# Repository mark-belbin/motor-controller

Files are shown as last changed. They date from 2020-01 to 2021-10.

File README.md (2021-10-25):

# FOC Motor Controller
This project was a multi-year effort to develop a ground-up, brushless motor (BLDC) controller for use in underwater robotics. 

The final controller is designed for T200 or T100 thrusters from BlueRobotics, boasting sensorless FOC and a miniature form-factor that is built right into the thruster.

## Key Features
- Sensorless FOC / sinusoidal commutation
- Input voltage up to 14V
- 250W Continuous Power
- CAN Bus telemetry and control
- Built into the T200 thruster, water-cooled
- Low underwater acoustic noise
- Up to 10-20% better efficiency than standard ESCs
- Great low-RPM operation and control
- *Ludicrous* mode, able to overmodulate and reach higher RPMs

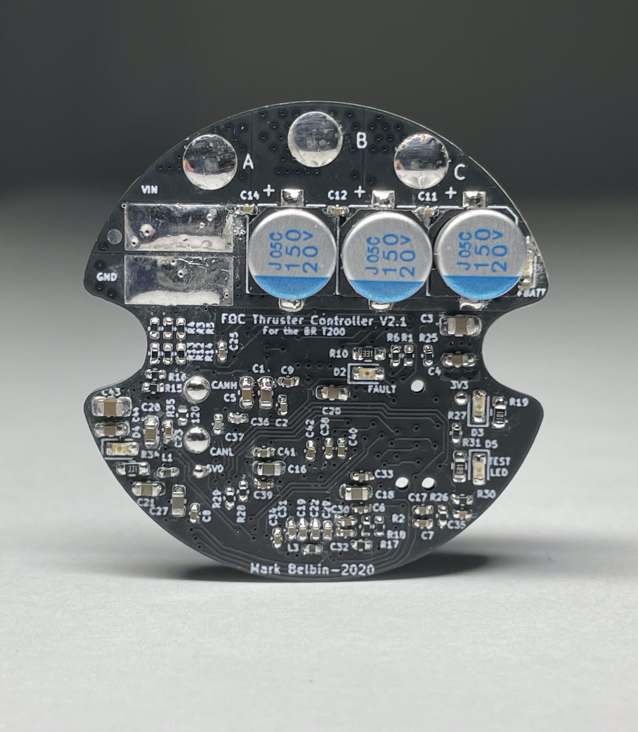
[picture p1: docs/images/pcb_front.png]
PCB Front


> FOC Thruster Controller V2 Top View

PCB Back

> FOC Thruster Controller V2 Bottom View

# Table of Contents
1. [Introduction](#Introduction)
1. [FOC Benefits](#FOC-Benefits)
   1. [Phase Currents](#Phase-Currents)
   1. [Operating Noise](#Operating-Noise)
   1. [Efficiency](#Efficiency)
   1. [Other Benefits](#Other-Benefits)
1. [Motor Controller PCB](#Motor-Controller-PCB)
1. [Controller Firmware](#Controller-Firmware)
1. [T200 Thruster Mount](#T200-Thruster-Mount)
1. [Repository Content](#Repository-Content)

# Introduction
Brushless motors, such as BLDC or PMSM motors, have no physical link between the stator and rotor like in a standard DC motor. Therefore, these motors must be commutated (spun properly) using an external controller. The key is knowing where the motor's rotor is relative to the stator, such that the magnetic field of the stator can be generated with accuracy in order to successfully push along the rotor and get the motor to spin. 

For most hobby BLDC controllers, commonly referred to as electronic speed controllers (ESCs), motor commutation is accomplished through sensorless trapezoidal 6-step control. This commutation method steps through 6 distinct stator magnetic field positions in order to keep the motor spinning, based only on the feedback of the back-EMF voltage of the three motor phases. With only 6 available control positions, this method of commutation lacks maximum possible efficiency, but it remains a simple, reliable, and cheap control method. 

This motor controller design implements Field-oriented control (FOC), also known as sinusoidal control or sine wave control. The FOC algorithm used is provided by Texas Instrument's InstaSPIN product line. This enables FOC using sensorless feedback, meaning no extra encoders or sensors are attached to the motor. The TI sensorless system measures only the 3 phase voltages and 3 phase currents of the motor in order to estimate the current rotor position with high accuracy. Also important is the intrinsic properties of the motor, such as the phase resistance, inductance, and the motor flux linkage. InstaSPIN requires a motor calibration procedure be run on each unique motor to automatically determine these intrinsic values, if not the FOC algorithm will not run.

This custom FOC controller design was evaluated by comparing against the BlueRobotics Basic ESC R3, a standard hobby-style ESC. Both will run the same BlueRobotics T200 thruster, which is the intended use-case of the custom developed controller. 

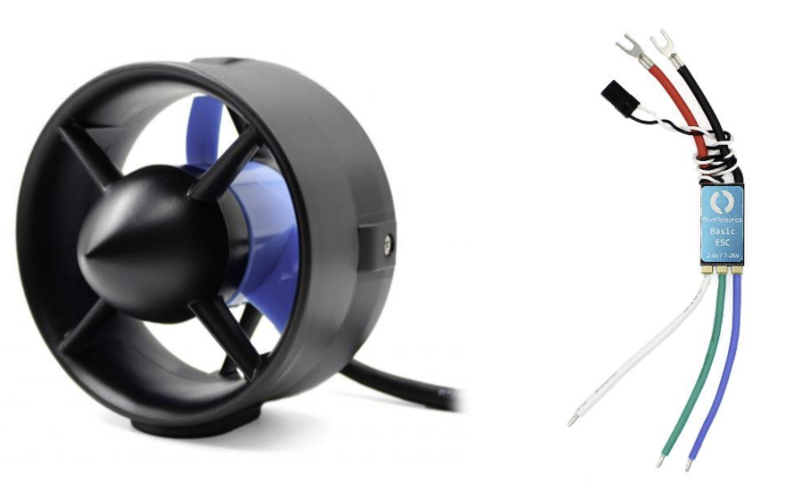
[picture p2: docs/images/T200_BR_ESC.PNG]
T200 and Basic ESC


> BlueRobotics T200 Thruster and Basic ESC R3.

# FOC Benefits
FOC has numerous potential benefits compared to traditional trapezoidal control. The most striking are the increase in efficiency and reduction in motor noise. This is possible since FOC control applies the most optimal stator magnetic field to push the rotor forward, and as a result generates clean and noise-free sine-wave current wave forms.

## Phase Currents

A comparison of current waveforms is shown below. Both the custom FOC controller and the Blue Robotics Basic ESC R3 are controlling a submerged T200 thruster at 2000 RPM. The FOC phase currents are much cleaner and closer to sinewaves, while the Basic ESC waveforms are more choppy and trapezoidal.

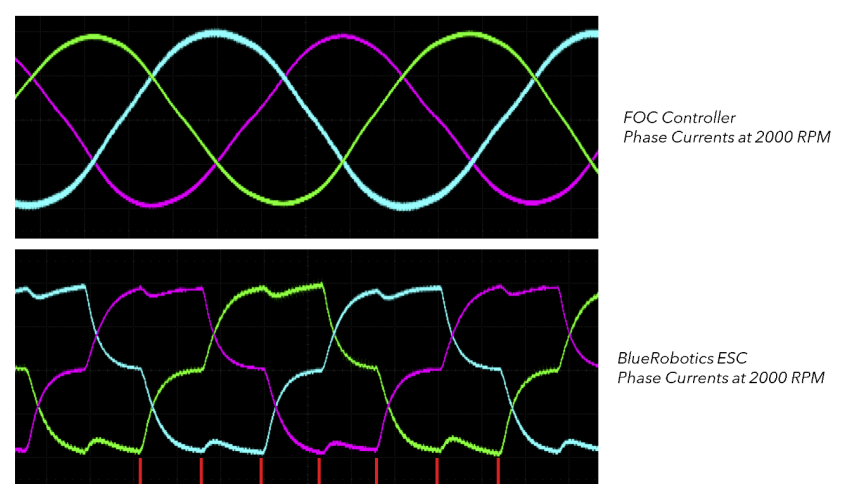
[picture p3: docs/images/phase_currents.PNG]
FOC Currents


> FOC phase currents vs the BR Basic ESC R3 at 2000 RPM.

## Operating Noise

A significant difference in operating noise is observed because of the current waveform difference. This is very noticeable underwater too, as the louder electrical sounds generated by the Basic ESC travel far. By comparison the custom FOC controller runs quiet, especially for low to mid-range speeds of 0-2000 RPM.

## Efficiency

An efficiency test was completed for both the custom and off-the-shelf controllers. A T200 was secured and submerged in a relatively large tub full of water. A separate waterproof, magnetic RPM sensor was attached to the shaft of the T200 to independently measure the RPM of the thruster. Measurements were taken of the input power of the motor controller under test for RPM settings in steps of 100 RPM.

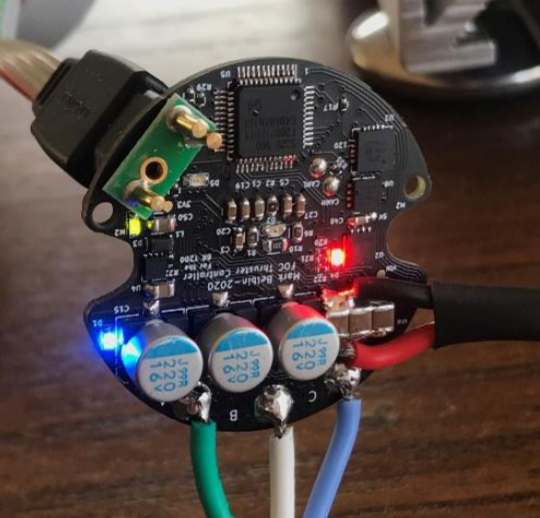
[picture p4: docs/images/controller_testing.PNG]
Controller Testing


> FOC Controller Testing

The FOC controller is more efficient across nearly the entire RPM range. The graph below is shows superiority up until about 2500 RPM, beyond which the FOC controller has the same or slightly worse performance. This is a limitation of FOC, where at a certain voltage the controller will switch to overmodulation control, where the controller will gradually transition to trapezoidal control as the RPM increases. To remain efficient at upper RPMs, a higher input voltage would need to be supplied.

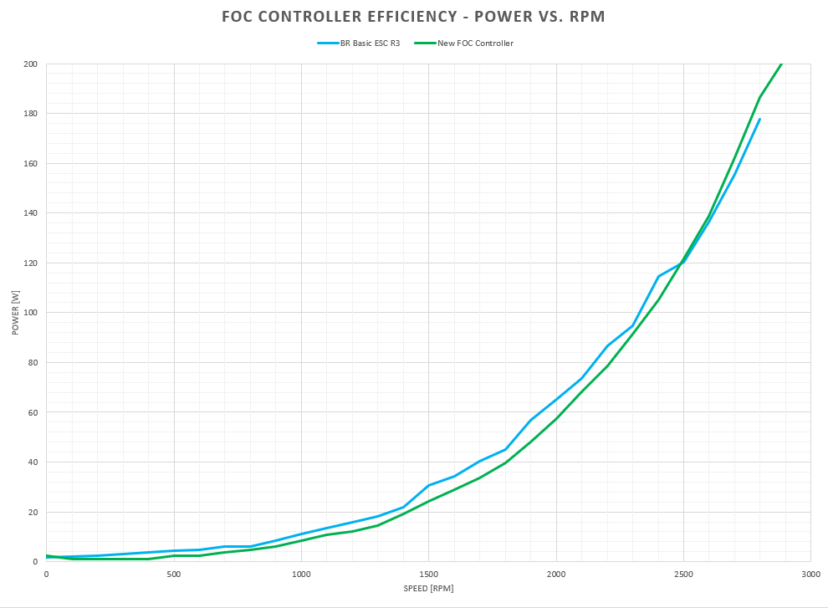
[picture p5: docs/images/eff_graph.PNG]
Efficiency Graph


> FOC Controller vs the BR Basic ESC R3.

Here's how the efficiency difference changes over the course of the RPM range: 

- From 0 to 600 RPM, the FOC controller consumes about 50% less power, a percent increase in efficiency of 100-150%
- From 600 to 1500 RPM, 20% less power is consumed, a percent increase in efficiency of 25-30%.
- From 1500 to 2000 RPM, 15% less power is consumed, a percent increase in efficiency of 15-20%.
- From 2000 to 2500 RPM, 5-10% less power is consumed, a percent increase in efficiency of 8-10%.
- Beyond 2500 RPM, the FOC controller consumes 0-5% more power than the Basic ESC.

The outperformance at lower RPMs is significant, since many underwater robotics applications operate in this range, such as Autonomous Underwater Vehicles (AUVs) or Autonomous Surface Vessels (ASVs). Battery life is critical for these types of vehicles, and the reduction in motor power from FOC control could have a big impact. 

## Other Benefits

A few other minor benefits were observed with the custom controller and FOC:

1. Great low speed control; The controller can operate at speeds down to a few RPM, where the Basic ESC cuts out under about 100 RPM.
2. Clean forward / reverse switching; During 0 RPM crossings, the FOC controller is much more stable, and can make these forward / reverse jumps with much quicker acceleration (about 25kRPM/s vs 14kRPM/s). This could improve position locking or increase accuracy for delicate maneuvers. 
3. *Ludicrous mode*; The FOC controller's overmodulation feature can push the thruster faster than the Basic ESC for the same input voltage, about 100 more RPM at 12V. Since thrust is proportional to the square of the RPM, this extra 100 RPM is a nice power boost.

# Motor Controller PCB
The motor controller PCB design was created using KiCAD. It's a 4 layer board, approximately in the shape of a xx diameter circle. The notches in the design allow it to be dropped in a mount for the T200 thruster. The PCB project is located in "hardware/Thruster_Controller_V2". An older version of the controller is found in "hardware/Thruster_Controller_V1", with the main difference being a different TI microcontroller.

PCB Angled

> FOC Thruster Controller V2 Angled View

The board itself is dense, and probably could have benefitted from a 6 layer design instead. However, limiting the design to 4 layers keeps the prototype costs very cheap. In total, for an order of 10 PCBAs, the total cost for the boards were about $2 each thanks to JLCPCB, and the total component cost is about $36.50 per board. So in total, less than $40 CAD per PCBA for only a 10 order quantity, not bad! At scale, this can shrink further, but probably not less than $25 per board.

Some major components are:
- TMS320F280041C -> TI microcontroller with InstaSPIN.
- DRV8320S -> Motor driver from TI.
- SIZF906DT -> Dual-MOSFETs in a compact package
- ATA6561 -> CAN Transceiver

# Controller Firmware
The controller firmware is based on MotorControl SDK 3.01 from TI. This SDK enables sensorless FOC with select TI microcontrollers. The microcontrollers have a proprietary InstaSPIN sensorless algorithm embedded in the ROM, which restricts this system to compatible TI MCUs only. 

The code is modified from a MotorControl SDK example lab, with extra drivers written for CAN communication. There is also some modification to disable a built-in overcurrent feature using the CMPSS. For whatever reason the feature seems to be bugged. I haven't yet figured out a good solution to either fix it or replace the overcurrent protection. So take caution if using this project as a base for something else! 

The IDE used is TIs Code Composer Studio, a customized version of Eclipse. The most up-to-date project is found in "firmware/TI_ESC_V2". The project is completely separated from TIs MotorControl SDK libraries, so it should be portable and importable in to Code Composer Studio from any computer with/without MotorControl SDK installed.

# T200 Thruster Mount
The motor controller PCBA was designed to be integrated into the back of the T200. The PCBA is first placed in an aluminum mount. Then, the thruster phase wires are soldered to the PCB. These wires are exposed by hacking away the jacket of the thruster very delicately. A new 10-conductor cable is then soldered to the PCB, replacing the original thruster cable. The final assembly is then potted, and mounted to the back of the thruster using the existing two screw holes originally for the back nose-cone. With this integration, the controller is water-cooled by the the thruster itself as water is forced passed it. 

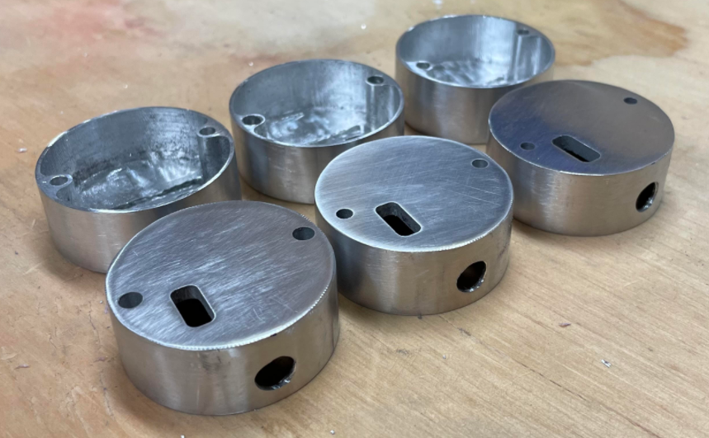
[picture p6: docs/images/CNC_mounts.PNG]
CNC Mounts


> Fresh-cut aluminum PCBA mounts

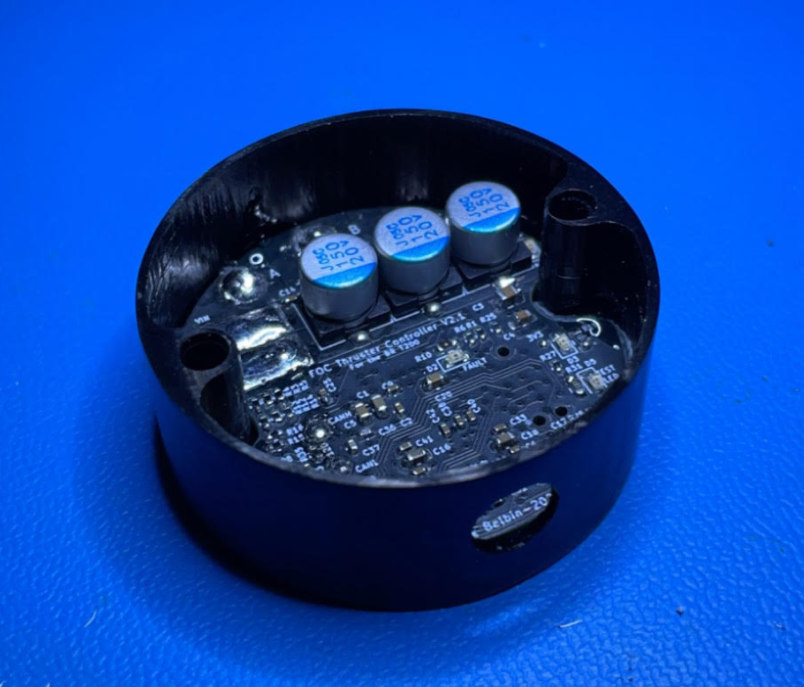
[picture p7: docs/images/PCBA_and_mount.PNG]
Controller Mount


> Anodized mount + PCBA

An interesting aspect of the mount design is the inclusion of a sealing disk. This disk, plus an o-ring, seals a programming port on the controller. This allows for reprogramming of the TI microcontroller while still maintaining water resistance. In the future it might be nice to include a bootloader on the microcontroller, which would allow programming over CAN instead, eliminating the need for this extra sealing disk! 

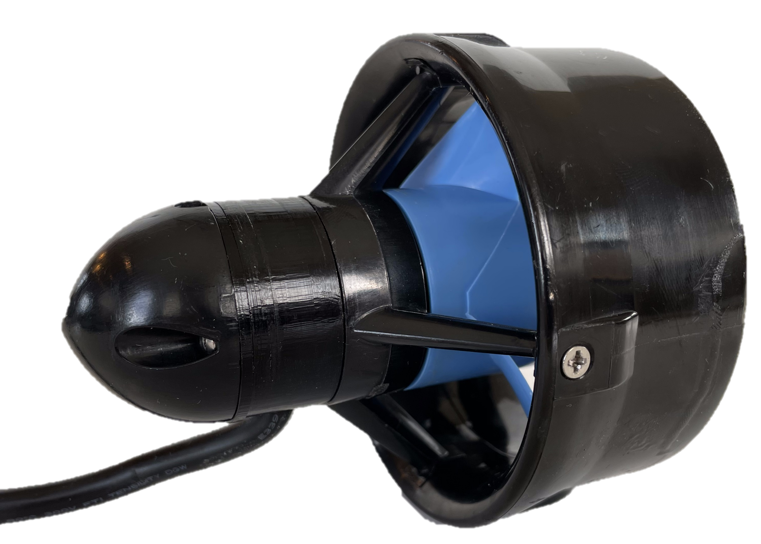
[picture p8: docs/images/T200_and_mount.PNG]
T200 + Controller Angled


> T200 + Controller Angled View

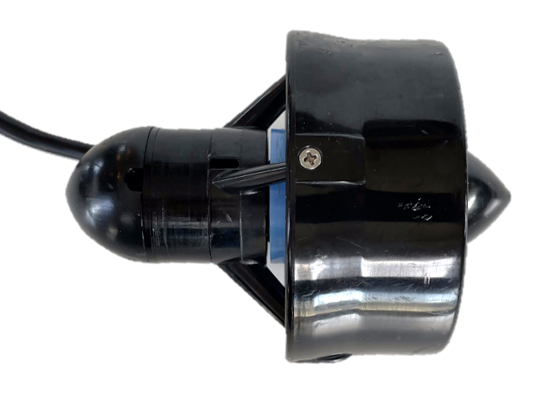
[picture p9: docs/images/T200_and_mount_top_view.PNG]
T200 + Controller Top


> T200 + Controller Top View

# AUV Integration

An immediate application of the FOC thruster controller was in my final-year engineering senior design project; an autonomous underwater vehicle (AUV). The AUV includes six thrusters in the design, and I built an FOC controller in each one. In the end, the project was a resounding success, and a very good test scenario for the custom controllers. The controllers were smooth, operating well at low speeds, which is all the AUV needed. The thrusters also operated very quietly, even when pushing the AUV to higher speeds for fun. 

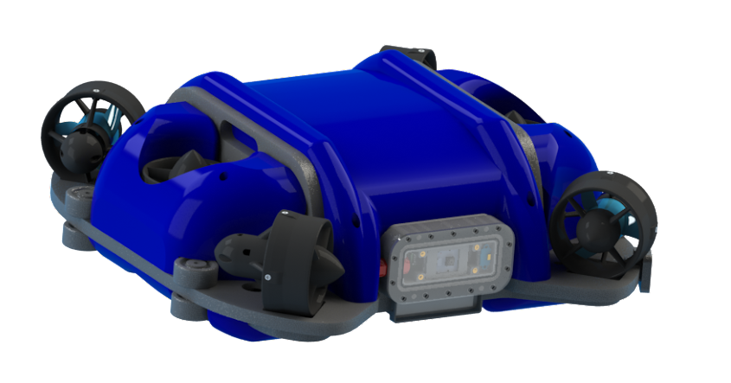
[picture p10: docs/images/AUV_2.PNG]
AUV Top


> Capstone AUV Top View

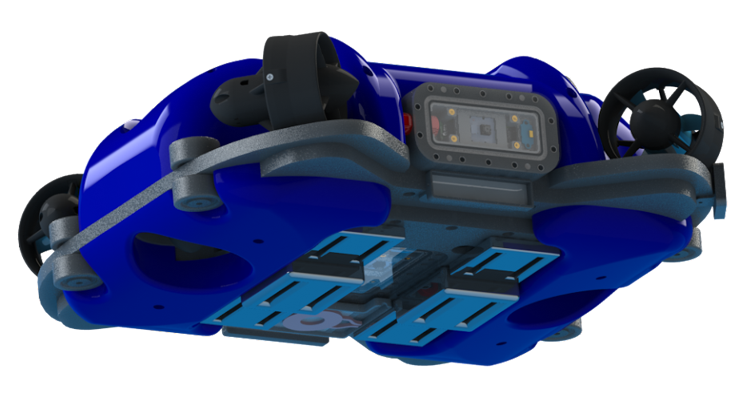
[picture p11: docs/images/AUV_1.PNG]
AUV Bottom


>  Capstone AUV Bottom View

Check out the AUV in action here -> https://www.youtube.com/watch?v=-c5bOXZom5M

# Repository Content
The repository is organized into 3 categories; hardware, firmware, and docs. Included in the hardware folder is the latest FOC controller V2, as well as an older version V1, and many test boards built to test and evaluate the project along the way. The firmware folder includes the latest V2 firmware, as well as the V1 firmware and sample test projects that were provided by TI and were useful for debugging.

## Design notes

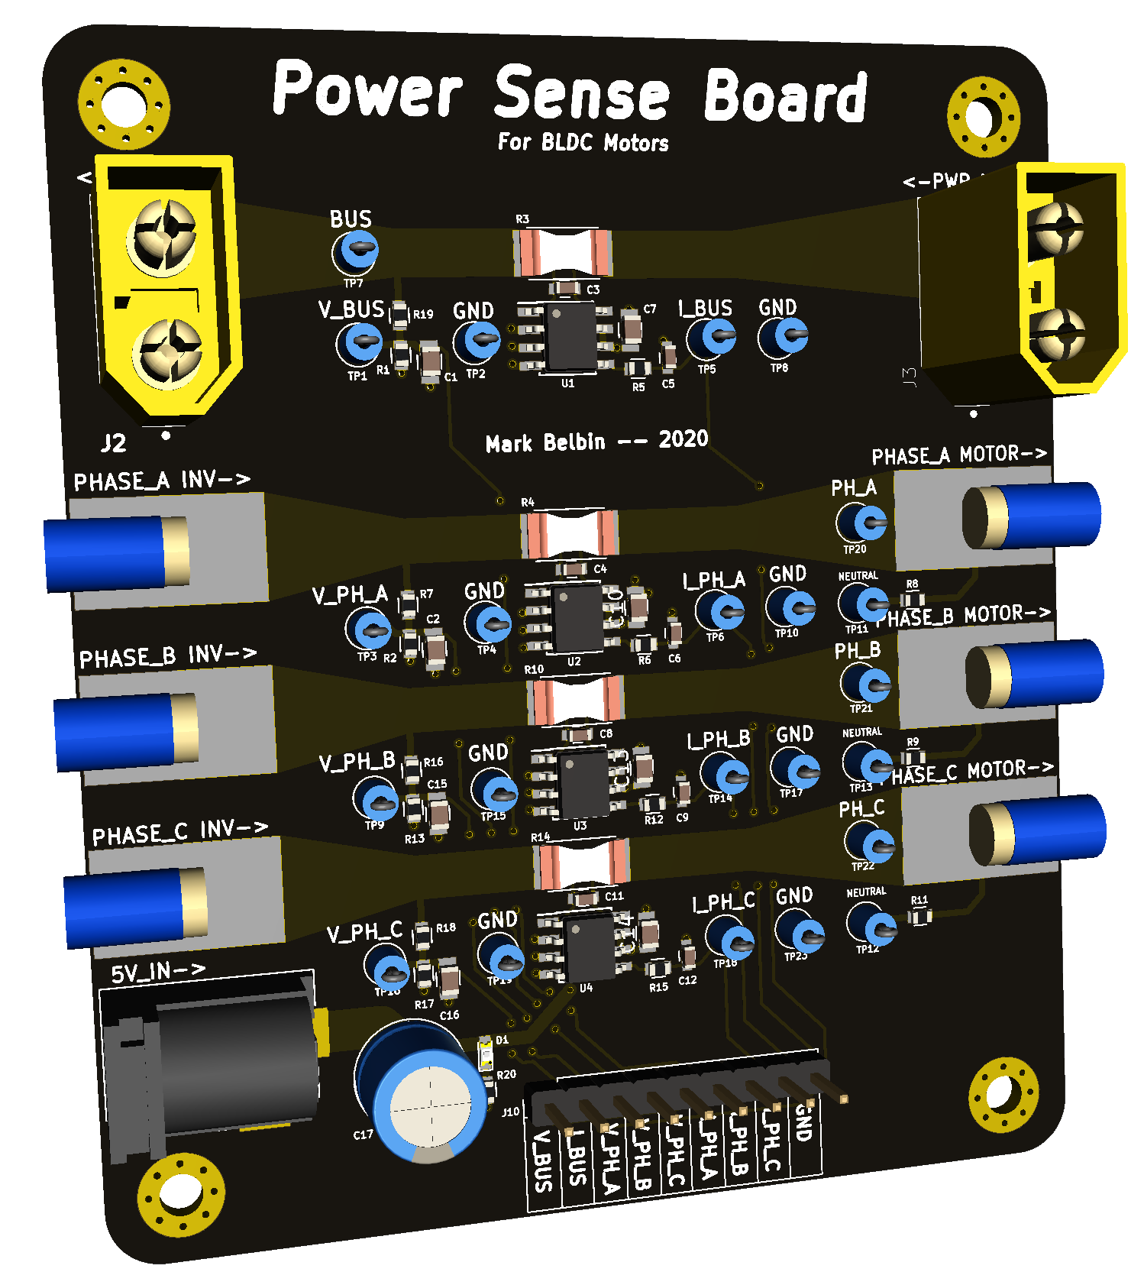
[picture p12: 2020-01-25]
hardware/Power Sense PCB/3D View.PNG

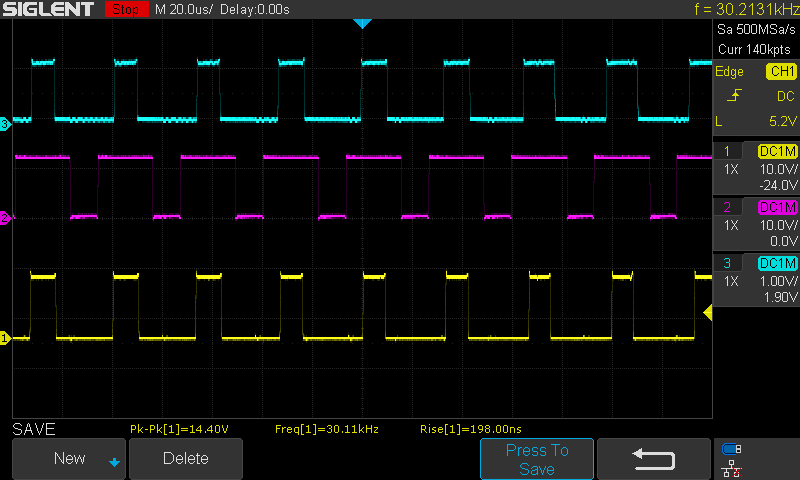
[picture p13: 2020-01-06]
hardware/ESC Drivetrain V1/Scope Shots/SDS00005.png

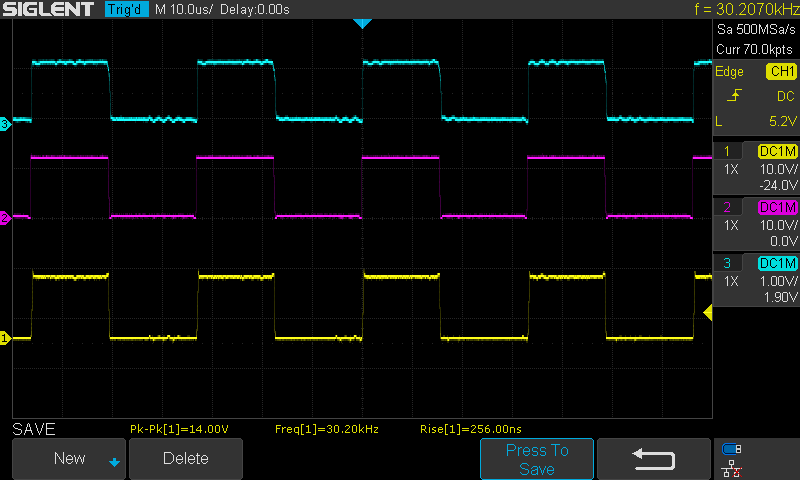
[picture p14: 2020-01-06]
hardware/ESC Drivetrain V1/Scope Shots/SDS00001.png

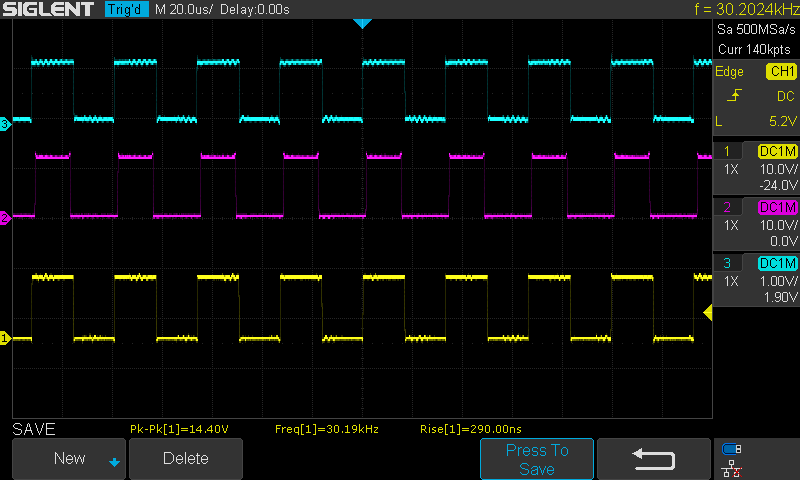
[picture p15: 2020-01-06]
hardware/ESC Drivetrain V1/Scope Shots/SDS00006.png

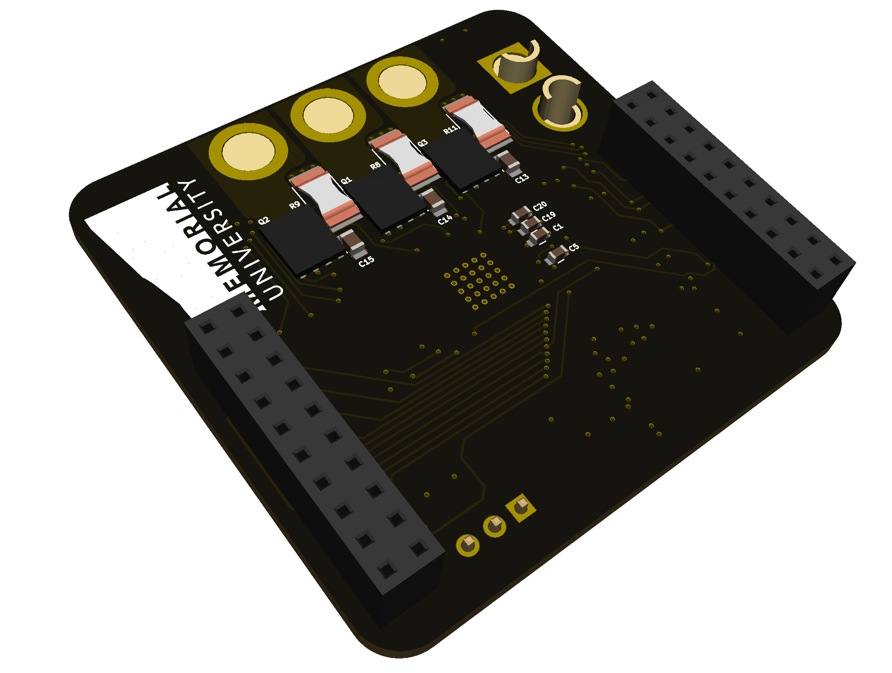
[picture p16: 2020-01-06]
hardware/ESC Drivetrain V1/3D View 2.PNG

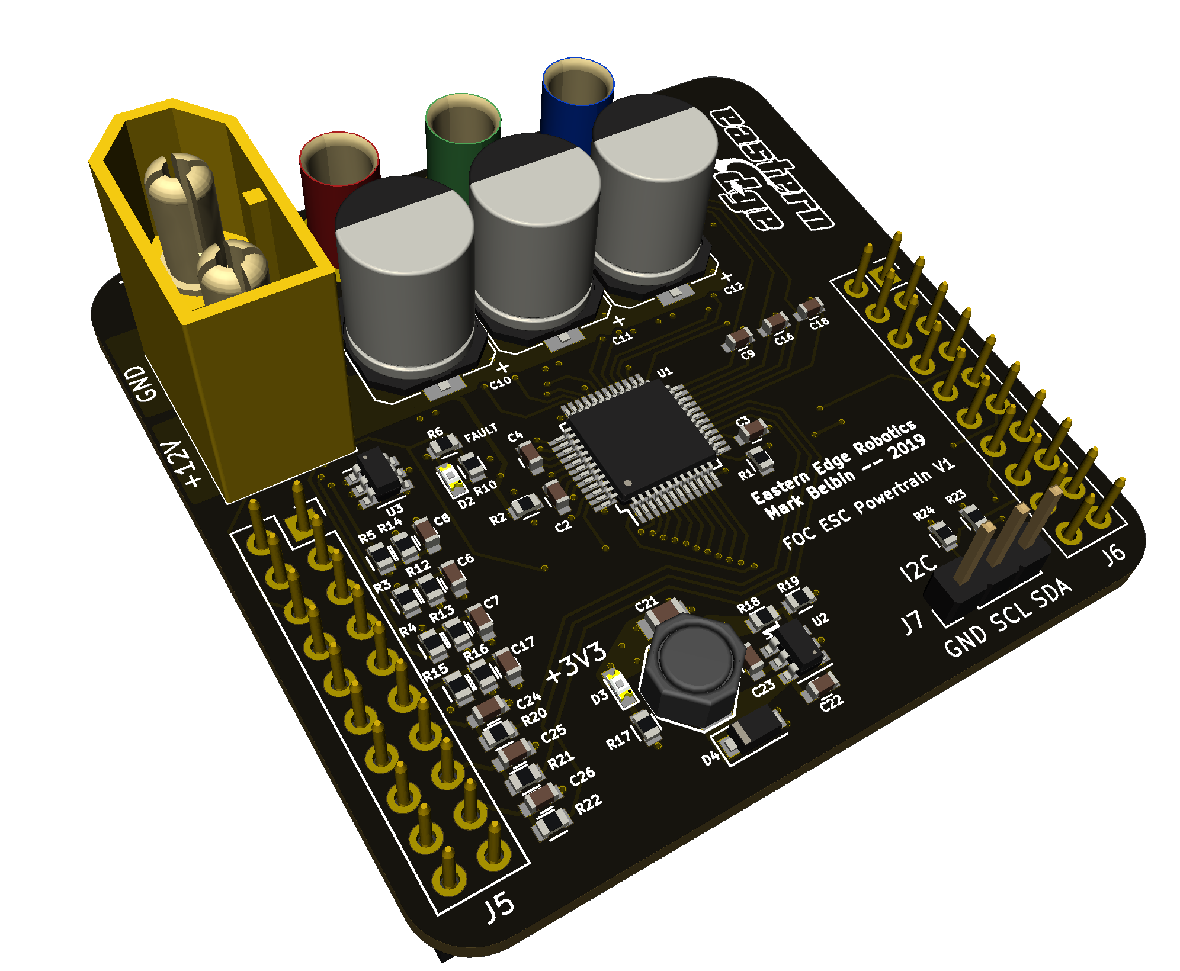
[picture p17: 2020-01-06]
hardware/ESC Drivetrain V1/3D View 1.PNG

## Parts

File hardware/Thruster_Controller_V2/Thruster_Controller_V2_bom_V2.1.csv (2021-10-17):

Component | Description | Part | References | Value | Footprint | Quantity Per PCB | Datasheet | Digikey | Voltage | Mouser
1 | Unpolarized capacitor, small symbol | C_Small | C11 C12 C14 C35 | 0.01uF | C_0402_1005Metric | 4 |  | 732-7545-1-ND
2 | Unpolarized capacitor, small symbol | C_Small | C2 | 0.047uF | C_0402_1005Metric | 1 |  | 490-10702-1-ND
3 | Unpolarized capacitor, small symbol | C_Small | C6 C7 C8 C9 C17 C23 C31 C33 C34 C38 C39 C40 C41 C42 | 0.1uF | C_0402_1005Metric | 14 |  | 490-10698-1-ND
4 | Unpolarized capacitor, small symbol | C_Small | C16 C18 C21 C27 | 10uF | C_0603_1608Metric | 4 | ~ | 1276-1119-1-ND
5 | Unpolarized capacitor, small symbol | C_Small | C4 C5 C20 C28 C44 | 1uF | C_0603_1608Metric | 5 |  | 1276-1102-1-ND
6 | Unpolarized capacitor, small symbol | C_Small | C3 C43 | 1uF | C_0805_2012Metric | 2 |  | 1276-6470-1-ND | 50V
7 | Unpolarized capacitor, small symbol | C_Small | C19 C22 C29 C30 C32 | 2.2uF | C_0402_1005Metric | 5 | ~ | 490-10451-1-ND
8 | Unpolarized capacitor, small symbol | C_Small | C24 C25 C26 | 2200pF | C_0402_1005Metric | 3 |  | 490-6359-1-ND
9 | Unpolarized capacitor | C | C10 C13 C15 | 220uF | CP_Elec_6.3x5.8 | 3 | ~ | 565-APXJ160ARA221MF61GCT-ND
10 | Unpolarized capacitor, small symbol | C_Small | C1 | 4.7uF | C_0603_1608Metric | 1 |  | 1276-1900-1-ND
11 | Unpolarized capacitor, small symbol | C_Small | C36 C37 | 9pF | C_0402_1005Metric | 2 | ~ | 490-5880-1-ND
12 | Light emitting diode, filled shape | LED_ALT | D1 | BLUE | LED_0603_1608Metric | 1 | ~ | 732-4966-1-ND
13 | Light emitting diode, filled shape | LED_ALT | D3 D4 | GREEN | LED_0603_1608Metric | 2 | ~ | 732-4980-1-ND
14 | Light emitting diode, filled shape | LED_ALT | D5 | Orange | LED_0603_1608Metric | 1 | ~ | 160-1180-1-ND
15 | Light emitting diode, filled shape | LED_ALT | D2 | RED | LED_0603_1608Metric | 1 | ~ | 732-4978-1-ND
16 | Generic connector, single row, 01x01, script generated (kicad-library-utils/schlib/autogen/connector/) | Conn_01x01 | J4 J6 | Conn_01x01 | CAN_Pad | 2 | ~
17 | Generic connector, single row, 01x01, script generated (kicad-library-utils/schlib/autogen/connector/) | Conn_01x01 | J7 J8 | Conn_01x01 | Bus_Pad | 2 | ~
18 | Generic connector, single row, 01x01, script generated (kicad-library-utils/schlib/autogen/connector/) | Conn_01x01 | J1 J2 J3 | PHASE_A | Phase_Pad | 3 | ~
19 | Generic connector, double row, 02x05, odd/even pin numbering scheme (row 1 odd numbers, row 2 even numbers), script generated (kicad-library-utils/schlib/autogen/connector/) | Conn_02x05_Odd_Even | J5 | Pogo Conn | Tag-Connect_TC2050-IDC-NL | 1 | ~
20 | Inductor, small symbol | L_Small | L1 | 220 Ohm | L_0402_1005Metric | 1 | ~ | 490-11021-1-ND
21 | Inductor, small symbol | L_Small | L3 | 60 Ohm | L_0402_1005Metric | 1 | ~ | 445-172882-1-ND
22 | Net tie, 2 pins | Net-Tie_2 | NT1 NT2 NT3 NT4 NT5 NT6 | Net-Tie_2 | NetTie-2_SMD_5mil | 6 | ~
23 |  | SIZF906DT | Q1 Q2 Q3 | SIZF906DT | SIZF906DT | 3 | http://www.vishay.com/docs/67547/sizf906dt.pdf | SIZF906DT-T1-GE3CT-ND
24 | Resistor, US symbol | R_US | R19 | 100 | R_0603_1608Metric | 1 | ~ | 2019-RK73B1JTTD101JCT-ND
25 | Resistor, US symbol | R_US | R6 R25 R26 R28 R29 | 10k | R_0402_1005Metric | 5 | ~ | 2019-RK73B1ETTP103JCT-ND
26 | Resistor, small US symbol | R_Small_US | R35 | 120 | R_0402_1005Metric | 1 | ~ | 311-120JRCT-ND
27 | Resistor, small US symbol | R_Small_US | R1 R27 R30 | 2.2k | R_0402_1005Metric | 3 | ~ | 311-2.2KJRCT-ND
28 | Resistor, US symbol | R_US | R23 R24 R32 | 2.49k | R_0402_1005Metric | 3 | ~ | RMCF0402FT2K49CT-ND
29 | Resistor, US symbol | R_US | R7 | 2.7k | R_0603_1608Metric | 1 | ~ | RMCF0603JT2K70CT-ND
30 | Resistor, US symbol | R_US | R3 R4 R5 R15 | 22.0k | R_0402_1005Metric | 4 | ~ | RMCF0402FT22K0CT-ND
31 | Resistor, US symbol | R_US | R34 | 220 | R_0603_1608Metric | 1 | ~ | 2019-RK73B1JTTD221JCT-ND
32 | Resistor, US symbol | R_US | R2 R17 R18 | 27.4k | R_0402_1005Metric | 3 | ~ | RMCF0402FT27K4CT-ND
33 | Resistor, US symbol | R_US | R10 | 330 | R_0603_1608Metric | 1 | ~ | RMCF0603JT330RCT-ND
34 | Resistor, US symbol | R_US | R12 R13 R14 R16 | 4.99k | R_0402_1005Metric | 4 | ~ | 311-4.99KLRCT-ND
35 | Resistor, US symbol | R_US | R20 R21 R22 R33 | 56 | R_0402_1005Metric | 4 | ~ | 311-56JRCT-ND
36 | Resistor, US symbol | R_US | R8 R9 R11 | 5m | R_2512_6332Metric | 3 |  | YAG6105CT-ND
37 | Resistor, US symbol | R_US | R31 | 680 | R_0603_1608Metric | 1 | ~ | RMCF0603JT680RCT-ND
38 | High-Speed CAN Transceiver, 1Mbps, 5V supply, Vio pin, -40C to +125C, DFN-8 | MCP2562-E-MF | U8 | ATA6561 | DFN-8-1EP_3x3mm_P0.65mm_EP1.7x2.05mm | 1 | https://ww1.microchip.com/downloads/en/DeviceDoc/20005991B.pdf | ATA6561-GBQW-NCT-ND |  | 579-ATA6561-GBQW-N
39 |  | DRV8320S | U3 | DRV8320S | WQFN-32-1EP_5x5mm_P0.5mm_EP3.1x3.1mm | 1 | http://www.ti.com/lit/ds/symlink/drv8323r.pdf?HQS=TI-null-null-mousermode-df-pf-null-wwe&DCM=yes&distId=26 | 296-50725-1-ND |  | 595-DRV8320SRTVR
40 |  | NCP718AMT330 | U1 | NCP718AMT330 | DFN-6-1EP_2x2mm_P0.65mm_EP1x1.6mm | 1 | https://www.mouser.ca/datasheet/2/308/NCP718-D-1224359.pdf | NCP718AMT330TBGOSCT-ND |  | 863-NCP718AMT330TBG
41 |  | NCP718AMT330 | U4 | NCP718AMT500 | DFN-6-1EP_2x2mm_P0.65mm_EP1x1.6mm | 1 | https://www.onsemi.com/pub/Collateral/NCP718-D.PDF | ‎NCP718AMT500TBGOSCT-ND‎ |  | 863-NCP718BMT500TBG
42 |  | TMS320F280041C | U2 | TMS320F280041C | QFN-56-1EP_7x7mm_P0.4mm_EP5.6x5.6mm | 1 | http://www.ti.com/lit/ds/symlink/tms320f280041.pdf?ts=1588432897241 | 296-F280041CRSHSRCT-ND |  | 595-F280041CRSHSR
43 | Three pin crystal, GND on pin 2 | Crystal_GND2 | Y1 | 20 MHz | Crystal_SMD_SeikoEpson_FA238-4pin_3.2x2.5mm | 1 | ~ | SER3629CT-ND
Component Groups: | 43
Component Count: | 109
Fitted Components: | 109
Number of PCBs: | 1
Total components: | 109
Schematic Version: | V2.1
Schematic Date: | 2020-09-04
PCB Variant: | [u'default']
BoM Date: | 2021-05-12 3:15:47 PM
Schematic Source: | D:\FOC_Motor_Controller\motor-controller\PCBs\Thruster_Controller_V2\Thruster_Controller_V2.sch
KiCad Version: | Eeschema (5.1.9)-1

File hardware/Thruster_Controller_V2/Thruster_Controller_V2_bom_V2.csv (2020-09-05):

Component | Description | Part | References | Value | Footprint | Quantity Per PCB | Datasheet | Digikey | Voltage | Mouser
1 | Unpolarized capacitor, small symbol | C_Small | C11 C12 C14 C35 | 0.01uF | C_0402 | 4 |  | 732-7545-1-ND
2 | Unpolarized capacitor, small symbol | C_Small | C2 | 0.047uF | C_0402 | 1 |  | 490-10702-1-ND
3 | Unpolarized capacitor, small symbol | C_Small | C6 C7 C8 C9 C17 C23 C31 C33 C34 C38 C39 C40 C41 C42 | 0.1uF | C_0402 | 14 |  | 490-10698-1-ND
4 | Unpolarized capacitor, small symbol | C_Small | C16 C18 C21 C27 | 10uF | C_0603 | 4 | ~ | 1276-1119-1-ND
5 | Unpolarized capacitor, small symbol | C_Small | C4 C5 C20 C28 | 1uF | C_0603 | 4 |  | 1276-1102-1-ND
6 | Unpolarized capacitor, small symbol | C_Small | C3 | 1uF | C_0805 | 1 |  | 1276-6470-1-ND | 50V
7 | Unpolarized capacitor, small symbol | C_Small | C19 C22 C29 C30 C32 | 2.2uF | C_0402 | 5 | ~ | 490-10451-1-ND
8 | Unpolarized capacitor, small symbol | C_Small | C24 C25 C26 | 2200pF | C_0402 | 3 |  | 490-6359-1-ND
9 | Unpolarized capacitor | C | C10 C13 C15 | 220uF | CP_Elec_6.3x5.8 | 3 | ~ | 565-APXJ160ARA221MF61GCT-ND
10 | Unpolarized capacitor, small symbol | C_Small | C1 | 4.7uF | C_0603 | 1 |  | 1276-1900-1-ND
11 | Unpolarized capacitor, small symbol | C_Small | C36 C37 | 9pF | C_0402 | 2 | ~ | 490-5880-1-ND
12 | Light emitting diode, filled shape | LED_ALT | D1 | BLUE | LED_0603 | 1 | ~ | 732-4966-1-ND
13 | Light emitting diode, filled shape | LED_ALT | D3 | GREEN | LED_0603 | 1 | ~ | 732-4980-1-ND
14 | Light emitting diode, filled shape | LED_ALT | D5 | Orange | LED_0603 | 1 | ~ | 160-1180-1-ND
15 | Light emitting diode, filled shape | LED_ALT | D2 | RED | LED_0603 | 1 | ~ | 732-4978-1-ND
16 | Generic connector, single row, 01x01, script generated (kicad-library-utils/schlib/autogen/connector/) | Conn_01x01 | J4 J6 | Conn_01x01 | CAN_Pad | 2 | ~
17 | Generic connector, single row, 01x01, script generated (kicad-library-utils/schlib/autogen/connector/) | Conn_01x01 | J7 J8 | Conn_01x01 | Bus_Pad | 2 | ~
18 | Generic connector, single row, 01x01, script generated (kicad-library-utils/schlib/autogen/connector/) | Conn_01x01 | J1 J2 J3 | PHASE_A | Phase_Pad | 3 | ~
19 | Generic connector, double row, 02x05, odd/even pin numbering scheme (row 1 odd numbers, row 2 even numbers), script generated (kicad-library-utils/schlib/autogen/connector/) | Conn_02x05_Odd_Even | J5 | Pogo Conn | Tag-Connect_TC2050-IDC-NL | 1 | ~
20 | Inductor, small symbol | L_Small | L1 | 220 Ohm | L_0402 | 1 | ~ | 490-11021-1-ND
21 | Inductor, small symbol | L_Small | L3 | 60 Ohm | L_0402 | 1 | ~ | 445-172882-1-ND
22 | Net tie, 2 pins | Net-Tie_2 | NT1 NT2 NT3 NT4 NT5 NT6 | Net-Tie_2 | NetTie-2_SMD_5mil | 6 | ~
23 |  | SIZF906DT | Q1 Q2 Q3 | SIZF906DT | SIZF906DT | 3 | http://www.vishay.com/docs/67547/sizf906dt.pdf | SIZF906DT-T1-GE3CT-ND
24 | Resistor, US symbol | R_US | R6 R25 R26 R28 R29 | 10k | R_0402 | 5 | ~ | 2019-RK73B1ETTP103JCT-ND
25 | Resistor, small US symbol | R_Small_US | R35 | 120 | R_0402 | 1 | ~ | 311-120JRCT-ND
26 | Resistor, US symbol | R_US | R19 | 180 | R_0603 | 1 | ~ | 2019-RK73B1JTTD181JCT-ND
27 | Resistor, small US symbol | R_Small_US | R1 R27 R30 | 2.2k | R_0402 | 3 | ~ | 311-2.2KJRCT-ND
28 | Resistor, US symbol | R_US | R23 R24 R32 | 2.49k | R_0402 | 3 | ~ | RMCF0402FT2K49CT-ND
29 | Resistor, US symbol | R_US | R7 | 2.7k | R_0603 | 1 | ~ | RMCF0603JT2K70CT-ND
30 | Resistor, US symbol | R_US | R3 R4 R5 R15 | 22.0k | R_0402 | 4 | ~ | RMCF0402FT22K0CT-ND
31 | Resistor, US symbol | R_US | R2 R17 R18 | 27.4k | R_0402 | 3 | ~ | RMCF0402FT27K4CT-ND
32 | Resistor, US symbol | R_US | R10 | 330 | R_0603 | 1 | ~ | RMCF0603JT330RCT-ND
33 | Resistor, US symbol | R_US | R12 R13 R14 R16 | 4.99k | R_0402 | 4 | ~ | 311-4.99KLRCT-ND
34 | Resistor, US symbol | R_US | R20 R21 R22 R33 | 56 | R_0402 | 4 | ~ | 311-56JRCT-ND
35 | Resistor, US symbol | R_US | R8 R9 R11 | 5m | R_2512 | 3 |  | YAG6105CT-ND
36 | Resistor, US symbol | R_US | R31 | 680 | R_0603 | 1 | ~ | RMCF0603JT680RCT-ND
37 |  | DRV8320S | U3 | DRV8320S | WQFN-32-1EP_5x5mm_Pitch0.5mm | 1 | http://www.ti.com/lit/ds/symlink/drv8323r.pdf?HQS=TI-null-null-mousermode-df-pf-null-wwe&DCM=yes&distId=26 | 296-50725-1-ND |  | 595-DRV8320SRTVR
38 | High-Speed CAN Transceiver, 1Mbps, 5V supply, Vio pin, -40C to +125C, DFN8 package | MCP2562-E-MF | U8 | MCP2562 | DFN-8-1EP_3x3mm_Pitch0.65mm | 1 | http://ww1.microchip.com/downloads/en/DeviceDoc/25167A.pdf | MCP2562-E/MF-ND
39 |  | NCP718AMT330 | U1 | NCP718AMT330 | DFN-6-1EP_2x2mm_Pitch0.65mm | 1 | https://www.mouser.ca/datasheet/2/308/NCP718-D-1224359.pdf | NCP718AMT330TBGOSCT-ND |  | 863-NCP718AMT330TBG
40 |  | TMS320F280041C | U2 | TMS320F280041C | QFN-56-1EP_7x7mm_Pitch0.4mm | 1 | http://www.ti.com/lit/ds/symlink/tms320f280041.pdf?ts=1588432897241 | 296-F280041CRSHSRCT-ND |  | 595-F280041CRSHSR
41 | Three pin crystal, GND on pin 2 | Crystal_GND2 | Y1 | 20 MHz | Crystal_SMD_SeikoEpson_FA238-4pin_3.2x2.5mm | 1 | ~ | SER3629CT-ND
Component Groups: | 41
Component Count: | 104
Fitted Components: | 104
Number of PCBs: | 1
Total components: | 104
Schematic Version: | V2
Schematic Date: | 2020-08-22
PCB Variant: | [u'default']
BoM Date: | 2020-08-22 4:44:00 PM
Schematic Source: | D:\Motor Controller Research\GitHub\motor-controller\PCBs\Thruster_Controller_V2\Thruster_Controller_V2.sch
KiCad Version: | Eeschema (5.1.5)-3

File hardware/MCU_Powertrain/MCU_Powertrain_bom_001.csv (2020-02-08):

Component | Description | Part | References | Value | Footprint | Quantity Per PCB | Datasheet | Digikey | Voltage
1 | Unpolarized capacitor, small symbol | C_Small | C2 C4 | 0.047uF | C_0402 | 2 |  | 490-10702-1-ND
2 | Unpolarized capacitor, small symbol | C_Small | C6 C7 C8 C17 C23 C30 C33 C42 | 0.1uF | C_0603 | 8 |  | 1276-CL10B104KB8NNNLCT-ND
3 | Unpolarized capacitor, small symbol | C_Small | C32 | 0.33uF | C_0603 | 1 |  | 1276-2370-1-ND
4 | Unpolarized capacitor, small symbol | C_Small | C39 | 1.01uF | C_0805 | 1 |  | 311-1909-1-ND | 35V
5 | Unpolarized capacitor, small symbol | C_Small | C9 C16 C18 | 1000pF | C_0402 | 3 |  | 311-1036-1-ND
6 | Unpolarized capacitor, small symbol | C_Small | C21 C22 | 15pF | C_0603 | 2 | ~ | 311-1060-1-ND
7 | Unpolarized capacitor, small symbol | C_Small | C3 C5 C20 C27 | 1uF | C_0603 | 4 |  | 1276-1102-1-ND
8 | Unpolarized capacitor, small symbol | C_Small | C28 C29 C40 C41 | 1uF | C_0805 | 4 |  | 399-8011-1-ND
9 | Unpolarized capacitor, small symbol | C_Small | C19 | 2.2uF | C_0603 | 1 |  | 490-10731-1-ND
10 | Unpolarized capacitor, small symbol | C_Small | C34 C35 C36 C37 C38 | 2.2uF | C_0805 | 5 | ~ | 1276-1763-1-ND
11 | Unpolarized capacitor, small symbol | C_Small | C24 C25 C26 | 2200pF | C_0603 | 3 |  | 490-1459-1-ND
12 | Polarized capacitor, US symbol | CP1 | C10 C11 C12 | 220uF | CP_Elec_8x10.5 | 3 |  | 25PEV220M8X10.5CT-ND
13 | Unpolarized capacitor, small symbol | C_Small | C13 C14 C15 C31 | 22uF | C_0805 | 4 |  | 490-14661-1-ND
14 | Unpolarized capacitor, small symbol | C_Small | C1 | 4.7uF | C_0603 | 1 |  | 1276-1900-1-ND
15 | Light emitting diode, filled shape | LED_ALT | D1 | BLUE | LED_0603 | 1 | ~ | 160-1827-1-ND
16 | Light emitting diode | LED | D5 D6 D7 D8 | BLUE | LED_0805 | 4 | ~ | 732-4982-1-ND
17 | Schottky diode, filled shape | D_Schottky_ALT | D4 | D_Schottky_ALT | D_SOD-123F | 1 | ~ | MBR1H100SFT3GOSCT-ND
18 | Light emitting diode, filled shape | LED_ALT | D3 | GREEN | LED_0603 | 1 | ~ | 160-1446-1-ND
19 | Light emitting diode, filled shape | LED_ALT | D2 | RED | LED_0603 | 1 | ~ | 160-1447-1-ND
20 | Generic connector, double row, 02x05, odd/even pin numbering scheme (row 1 odd numbers, row 2 even numbers), script generated (kicad-library-utils/schlib/autogen/connector/) | Conn_02x05_Odd_Even | J4 | Big Conn | 2x05_Prog_Header | 1 | ~ | 302-S101
21 | Generic connector, single row, 01x03, script generated (kicad-library-utils/schlib/autogen/connector/) | Conn_01x03 | J6 | Conn CAN | 70553-03 | 1 | ~ | WM4901-ND
22 | Generic connector, single row, 01x01, script generated (kicad-library-utils/schlib/autogen/connector/) | Conn_01x01 | J1 J2 J3 | PHASE_A | 3mm_Bullet_RA | 3 | ~
23 | Generic connector, single row, 01x02, script generated (kicad-library-utils/schlib/autogen/connector/) | Conn_01x02 | J7 | PWRIN | AMASS_XT60-M | 1 | ~
24 | Generic connector, double row, 02x05, odd/even pin numbering scheme (row 1 odd numbers, row 2 even numbers), script generated (kicad-library-utils/schlib/autogen/connector/) | Conn_02x05_Odd_Even | J5 | Pogo Conn | Tag-Connect_TC2050-IDC-NL | 1 | ~
25 | Inductor with ferrite core | L_Core_Ferrite | L1 | 15uH | Eaton_Inductor | 1 | ~ | 513-1458-1-ND
26 | Inductor, small symbol | L_Small | L2 | FB | L_0805 | 1 | ~ | 240-2549-1-ND
27 | Inductor, small symbol | L_Small | L3 | FB | L_0402 | 1 | ~ | 445-172882-1-ND
28 | Net tie, 2 pins | Net-Tie_2 | NT1 NT2 NT3 NT4 NT5 NT6 | Net-Tie_2 | NetTie-2_SMD_5mil | 6 | ~
29 |  | SIZF906DT | Q1 Q2 Q3 | SIZF906DT | SIZF906DT | 3 | http://www.vishay.com/docs/67547/sizf906dt.pdf | SIZF906DT-T1-GE3CT-ND
30 | Resistor, US symbol | R_US | R2 | 100 | R_0603 | 1 | ~ | RHM100DCT-ND
31 | Resistor, US symbol | R_US | R1 R6 | 10k | R_0603 | 2 | ~ | RNCP0603FTD10K0CT-ND
32 | Resistor, small US symbol | R_Small_US | R17 R18 | 10k | R_0805 | 2 | ~ | 311-10.0KCRCT-ND
33 | Resistor, small US symbol | R_Small_US | R35 | 120 | R_0805 | 1 | ~ | A129738CT-ND
34 | Resistor, small US symbol | R_Small_US | R27 R28 R29 R30 | 2.2k | R_0805 | 4 | ~ | 541-4139-1-ND
35 | Resistor, US symbol | R_US | R7 | 2.7k | R_0603 | 1 | ~ | P2.7KDACT-ND
36 | Resistor, US symbol | R_US | R24 | 20.0k | R_0603 | 1 | ~ | P20KDBCT-ND
37 | Resistor, US symbol | R_US | R3 R4 R5 R15 | 22.0k | R_0603 | 4 | ~ | P22KDBCT-ND
38 | Resistor, US symbol | R_US | R10 R19 | 330 | R_0603 | 2 | ~ | RHM330DCT-ND
39 | Resistor, small US symbol | R_Small_US | R31 R32 R33 R34 | 330 | R_0805 | 4 | ~ | A129743CT-ND
40 | Resistor, US symbol | R_US | R12 R13 R14 R16 | 4.99k | R_0603 | 4 | ~ | P4.99KDBCT-ND
41 | Resistor, US symbol | R_US | R20 R21 R22 | 56 | R_0603 | 3 | ~ | A129673CT-ND
42 | Resistor, US symbol | R_US | R8 R9 R11 | 5m | R_2512_Sense | 3 |  | YAG6124CT-ND
43 | Resistor, US symbol | R_US | R23 | 68.0k | R_0603 | 1 | ~ | P68KDBCT-ND
44 | Resistor, small US symbol | R_Small_US | R25 R26 | 820 | R_0805 | 2 | ~ | 311-820ARCT-ND
45 | Push button switch, generic, two pins | SW_Push | SW1 SW2 | SW_Push | SW_SPST_EVQQ2 | 2 | ~ | CKN9112CT-ND
46 |  | DRV8305 | U1 | DRV8305 | DRV8305 | 1 | http://www.ti.com/lit/ds/symlink/drv8305.pdf | 296-42659-1-ND
47 |  | LMR16006XDDC | U4 | LMR16006XDDC | SOT-23-6 | 1 | http://www.ti.com/lit/ds/symlink/lmr16006.pdf | 296-40293-1-ND
48 | Stand-Alone CAN Controller with SPI Interface, TSSOP-20 | MCP2515-QFN20 | U3 | MCP2515 | QFN-20-1EP_4x4mm_Pitch0.5mm | 1 | http://ww1.microchip.com/downloads/en/DeviceDoc/21801e.pdf | MCP2515T-I/MLCT-ND
49 | High-Speed CAN Transceiver, 1Mbps, 5V supply, Vio pin, -40C to +125C, DFN8 package | MCP2562-E-MF | U8 | MCP2562 | DFN-8-1EP_3x3mm_Pitch0.65mm | 1 | http://ww1.microchip.com/downloads/en/DeviceDoc/25167A.pdf | MCP2562-E/MF-ND
50 |  | RTQ2569-50GQW | U2 | RTQ2569-50GQW | DFN-8-1EP_3x3mm_Pitch0.65mm | 1 |  | 1028-1523-1-ND
51 | Dual-Bit Dual-Supply Bus Transceiver With Configurable Voltage Translation and 3-State Outputs, VSSOP-8 | SN74LVC2G07 | U6 U7 | SN74LVC2G07 | VSSOP-8_2.4x2.1mm_Pitch0.5mm | 2 | http://www.ti.com/lit/ds/symlink/sn74lvc2t45.pdf | 296-13494-1-ND
52 |  | TMS320F28027F | U5 | TMS320F28027F | LQFP-48_7x7mm_Pitch0.5mm | 1 |  | 296-36409-ND
53 | Four pin crystal, GND on pins 2 and 4 | Crystal_GND24 | Y1 | 20MHz | Crystal_SMD_SeikoEpson_TSX3225-4pin_3.2x2.5mm | 1 | ~ | SER4249CT-ND
Component Groups: | 53
Component Count: | 115
Fitted Components: | 115
Number of PCBs: | 1
Total components: | 115
Schematic Version: | 001
Schematic Date: | 2020-01-15
PCB Variant: | [u'default']
BoM Date: | 2020-02-07 8:15:42 PM
Schematic Source: | D:\Motor Controller Research\GitHub\motor-controller\PCBs\MCU_Powertrain\MCU_Powertrain.sch
KiCad Version: | Eeschema (5.1.5)-3

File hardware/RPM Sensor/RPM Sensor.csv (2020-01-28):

Source: | D:\Motor Controller Research\GitHub\motor-controller\PCBs\RPM Sensor\RPM Sensor.sch
Date: | 01/28/20 19:10:07
Tool: | Eeschema (5.1.5)-3
Generator: | C:\Program Files\KiCad\bin\scripting\plugins/bom_csv_grouped_by_value.py
Component Count: | 23
Individual Components:
Item | Qty | Reference(s) | Value | LibPart | Footprint | Datasheet | Digikey
 |  | C1 | 100uF | Device:CP | Capacitors_Tantalum_SMD:CP_Tantalum_Case-U_EIA-6032-15_Reflow | ~ | 478-7995-1-ND
 |  | C2 | 100uF | Device:CP | Capacitors_Tantalum_SMD:CP_Tantalum_Case-U_EIA-6032-15_Reflow | ~ | 478-7995-1-ND
 |  | C3 | 0.1uF | Device:C_Small | Capacitors_SMD:C_0805 | ~ | 311-1361-1-ND
 |  | C4 | 10uF | Device:C_Small | Capacitors_SMD:C_0805 | ~ | 399-4925-1-ND
 |  | H1 | MountingHole | Mechanical:MountingHole | Mounting_Holes:MountingHole_3.2mm_M3_ISO14580 | ~
 |  | H2 | MountingHole | Mechanical:MountingHole | Mounting_Holes:MountingHole_3.2mm_M3_ISO14580 | ~
 |  | J1 | I | Connector_Generic:Conn_01x01 | Testpoints:TestPoint_Pad_D2.0mm | ~
 |  | J2 | B | Connector_Generic:Conn_01x01 | Testpoints:TestPoint_Pad_D2.0mm | ~
 |  | J3 | I | Connector_Generic:Conn_01x01 | Testpoints:TestPoint_Pad_D2.0mm | ~
 |  | J4 | A | Connector_Generic:Conn_01x01 | Testpoints:TestPoint_Pad_D2.0mm | ~
 |  | J5 | U | Connector_Generic:Conn_01x01 | Testpoints:TestPoint_Pad_D2.0mm | ~
 |  | J6 | V | Connector_Generic:Conn_01x01 | Testpoints:TestPoint_Pad_D2.0mm | ~
 |  | J7 | W/PWM | Connector_Generic:Conn_01x01 | Testpoints:TestPoint_Pad_D2.0mm | ~
 |  | J8 | SCL/CLK | Connector_Generic:Conn_01x01 | Testpoints:TestPoint_Pad_D2.0mm | ~
 |  | J9 | NSL/DI | Connector_Generic:Conn_01x01 | Testpoints:TestPoint_Pad_D2.0mm | ~
 |  | J10 | DO/DO | Connector_Generic:Conn_01x01 | Testpoints:TestPoint_Pad_D2.0mm | ~
 |  | J11 | SEL/SEL | Connector_Generic:Conn_01x01 | Testpoints:TestPoint_Pad_D2.0mm | ~
 |  | J12 | I | Connector_Generic:Conn_01x01 | Testpoints:TestPoint_Pad_D2.0mm | ~
 |  | J13 | I | Connector_Generic:Conn_01x01 | Testpoints:TestPoint_Pad_D2.0mm | ~
 |  | J14 | I | Connector_Generic:Conn_01x01 | Testpoints:TestPoint_Pad_D2.0mm | ~
 |  | J15 | I | Connector_Generic:Conn_01x01 | Testpoints:TestPoint_Pad_D2.0mm | ~
 |  | J16 | I | Connector_Generic:Conn_01x01 | Testpoints:TestPoint_Pad_D2.0mm | ~
 |  | U1 | MAG_ENCODER_AEAT-8800-Q24 | RPM_Sensor:MAG_ENCODER_AEAT-8800-Q24 | Housings_DFN_QFN:QFN-24-1EP_4x4mm_Pitch0.5mm |  | 516-3787-ND
Collated Components:
Item | Qty | Reference(s) | Value | LibPart | Footprint | Datasheet | Digikey
1 | 2 | C1, C2 | 100uF | Device:CP | Capacitors_Tantalum_SMD:CP_Tantalum_Case-U_EIA-6032-15_Reflow | ~ | 478-7995-1-ND
2 | 1 | C3 | 0.1uF | Device:C_Small | Capacitors_SMD:C_0805 | ~ | 311-1361-1-ND
3 | 1 | C4 | 10uF | Device:C_Small | Capacitors_SMD:C_0805 | ~ | 399-4925-1-ND
4 | 2 | H1, H2 | MountingHole | Mechanical:MountingHole | Mounting_Holes:MountingHole_3.2mm_M3_ISO14580 | ~
5 | 7 | J1, J3, J12, J13, J14, J15, J16 | I | Connector_Generic:Conn_01x01 | Testpoints:TestPoint_Pad_D2.0mm | ~
6 | 1 | J2 | B | Connector_Generic:Conn_01x01 | Testpoints:TestPoint_Pad_D2.0mm | ~
7 | 1 | J4 | A | Connector_Generic:Conn_01x01 | Testpoints:TestPoint_Pad_D2.0mm | ~
8 | 1 | J5 | U | Connector_Generic:Conn_01x01 | Testpoints:TestPoint_Pad_D2.0mm | ~
9 | 1 | J6 | V | Connector_Generic:Conn_01x01 | Testpoints:TestPoint_Pad_D2.0mm | ~
10 | 1 | J7 | W/PWM | Connector_Generic:Conn_01x01 | Testpoints:TestPoint_Pad_D2.0mm | ~
11 | 1 | J8 | SCL/CLK | Connector_Generic:Conn_01x01 | Testpoints:TestPoint_Pad_D2.0mm | ~
12 | 1 | J9 | NSL/DI | Connector_Generic:Conn_01x01 | Testpoints:TestPoint_Pad_D2.0mm | ~
13 | 1 | J10 | DO/DO | Connector_Generic:Conn_01x01 | Testpoints:TestPoint_Pad_D2.0mm | ~
14 | 1 | J11 | SEL/SEL | Connector_Generic:Conn_01x01 | Testpoints:TestPoint_Pad_D2.0mm | ~
15 | 1 | U1 | MAG_ENCODER_AEAT-8800-Q24 | RPM_Sensor:MAG_ENCODER_AEAT-8800-Q24 | Housings_DFN_QFN:QFN-24-1EP_4x4mm_Pitch0.5mm |  | 516-3787-ND

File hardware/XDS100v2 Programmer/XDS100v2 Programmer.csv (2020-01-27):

Source: | D:\Motor Controller Research\GitHub\motor-controller\PCBs\XDS100v2 Programmer\XDS100v2 Programmer.sch
Date: | 2020-01-14 16:15
Tool: | Eeschema (5.1.5)-3
Generator: | C:\Program Files\KiCad\bin\scripting\plugins/bom_csv_grouped_by_value.py
Component Count: | 46
Item | Qty | Reference(s) | Value | LibPart | Footprint | Datasheet | Digikey
1 | 2 | C1, C2 | 4.7uF | Device:C_Small | Capacitors_SMD:C_0805 | ~ | 490-14466-1-ND
2 | 1 | C3 | 1uF | Device:C_Small | Capacitors_SMD:C_0805 | ~ | 399-8011-1-ND
3 | 1 | C4 | 100uF | Device:CP |  | ~ | 478-7995-1-ND
4 | 6 | C5, C6, C7, C8, C10, C11 | 0.1uF | Device:C_Small | Capacitors_SMD:C_0805 | ~ | 311-1361-1-ND
5 | 1 | C9 | 3.3uF | Device:C_Small | Capacitors_SMD:C_0805 | ~ | 490-13309-1-ND
6 | 2 | C12, C13 | 36p | Device:C_Small | Capacitors_SMD:C_0603 | ~ | 490-1416-1-ND
7 | 3 | D1, D2, D3 | LED | Device:LED | LEDs:LED_0805 | ~ | 475-1278-1-ND
8 | 1 | F1 | 500mA | Device:Fuse |  | ~ | MF-MSMF050-2CT-ND
9 | 1 | J1 | USB_B_Mini | Connector:USB_B_Mini |  | ~ | ED2992CT-ND
10 | 1 | J2 | Conn_02x05 | Connector_Generic:Conn_02x05_Counter_Clockwise |  | ~ | ED1543-ND
11 | 2 | L1, L2 | FB | Device:L | Inductors_SMD:L_0402 | ~ | 553-2374-1-ND
12 | 3 | R1, R3, R4 | 1k | Device:R_Small_US | Resistors_SMD:R_0805 | ~ | 311-1.0KARCT-ND
13 | 2 | R2, R7 | 10k | Device:R_Small_US | Resistors_SMD:R_0805 | ~ | 311-10.0KCRCT-ND
14 | 5 | R5, R10, R13, R14, R15 | 2.2k | Device:R_Small_US | Resistors_SMD:R_0805 | ~ | 311-2.20KCRCT-ND
15 | 1 | R6 | 12k | Device:R_Small_US | Resistors_SMD:R_0805 | ~ | A129762CT-ND
16 | 2 | R8, R9 | 330 | Device:R_Small_US | Resistors_SMD:R_0805 | ~ | A129743CT-ND
17 | 2 | R11, R12 | 820 | Device:R_Small_US | Resistors_SMD:R_0805 | ~ | 311-820ARCT-ND
18 | 2 | SW1, SW2 | SW_DIP_x02 | Switch:SW_DIP_x02 |  | ~ | CT204211ST-ND
19 | 1 | SW3 | SW_DIP_x03 | Switch:SW_DIP_x03 |  | ~ | CT2043ST-ND
20 | 1 | U1 | TLV1117-33 | Regulator_Linear:TLV1117-33 | TO_SOT_Packages_SMD:SOT-223 | http://www.ti.com/lit/ds/symlink/tlv1117.pdf | 296-50648-ND
21 | 1 | U2 | ISO7240 | XDS100v2 Programmer:ISO7240 | Housings_SOIC:SOIC-16W_7.5x10.3mm_Pitch1.27mm |  | 296-22617-1-ND
22 | 1 | U3 | EEPROM_Array | XDS100v2 Programmer:EEPROM_Array | TO_SOT_Packages_SMD:SOT-23-6
23 | 1 | U4 | FT2232H | Interface_USB:FT2232H | Housings_DFN_QFN:QFN-64-1EP_9x9mm_Pitch0.5mm | https://www.ftdichip.com/Support/Documents/DataSheets/ICs/DS_FT2232H.pdf | 768-1025-1-ND
24 | 1 | U5 | ISO7231 | XDS100v2 Programmer:ISO7231 | Housings_SOIC:SOIC-16W_7.5x10.3mm_Pitch1.27mm |  | 296-22960-5-ND
25 | 1 | U6 | EEPROM_Array_8pin | XDS100v2 Programmer:EEPROM_Array_8pin |  |  | 1662-2080-1-ND
26 | 1 | Y1 | 12MHz | Device:Crystal_Small |  | ~ | XC2079CT-ND

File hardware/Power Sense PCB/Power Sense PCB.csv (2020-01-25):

Source: | D:\Motor Controller Research\GitHub\motor-controller\PCBs\Power Sense PCB\Power Sense PCB.sch
Date: | 2020-01-23 10:59:36 PM
Tool: | Eeschema (5.1.5)-3
Generator: | C:\Program Files\KiCad\bin\scripting\plugins/bom_csv_grouped_by_value.py
Component Count: | 61
Individual Components:
Item | Qty | Reference(s) | Value | LibPart | Footprint | Datasheet | Digikey
 |  | C1 | 0.1uF | Device:C_Small | Capacitors_SMD:C_0805 | ~ | 478-12799-1-ND
 |  | C2 | 0.1uF | Device:C_Small | Capacitors_SMD:C_0805 | ~ | 478-12799-1-ND
 |  | C3 | C_Small | Device:C_Small | Capacitors_SMD:C_0603 | ~
 |  | C4 | C_Small | Device:C_Small | Capacitors_SMD:C_0603 | ~
 |  | C5 | C_Small | Device:C_Small | Capacitors_SMD:C_0603 | ~
 |  | C6 | C_Small | Device:C_Small | Capacitors_SMD:C_0603 | ~
 |  | C7 | 0.1uF | Device:C_Small | Capacitors_SMD:C_0805 | ~ | 478-12799-1-ND
 |  | C8 | C_Small | Device:C_Small | Capacitors_SMD:C_0603 | ~
 |  | C9 | C_Small | Device:C_Small | Capacitors_SMD:C_0603 | ~
 |  | C10 | 0.1uF | Device:C_Small | Capacitors_SMD:C_0805 | ~ | 478-12799-1-ND
 |  | C11 | C_Small | Device:C_Small | Capacitors_SMD:C_0603 | ~
 |  | C12 | C_Small | Device:C_Small | Capacitors_SMD:C_0603 | ~
 |  | C13 | 0.1uF | Device:C_Small | Capacitors_SMD:C_0805 | ~ | 478-12799-1-ND
 |  | C14 | 0.1uF | Device:C_Small | Capacitors_SMD:C_0805 | ~ | 478-12799-1-ND
 |  | C15 | 0.1uF | Device:C_Small | Capacitors_SMD:C_0805 | ~ | 478-12799-1-ND
 |  | C16 | 0.1uF | Device:C_Small | Capacitors_SMD:C_0805 | ~ | 478-12799-1-ND
 |  | H1 | MountingHole | Mechanical:MountingHole | Mounting_Holes:MountingHole_3mm_Pad_Via | ~
 |  | H2 | MountingHole | Mechanical:MountingHole | Mounting_Holes:MountingHole_3mm_Pad_Via | ~
 |  | H3 | MountingHole | Mechanical:MountingHole | Mounting_Holes:MountingHole_3mm_Pad_Via | ~
 |  | H4 | MountingHole | Mechanical:MountingHole | Mounting_Holes:MountingHole_3mm_Pad_Via | ~
 |  | J1 | Jack-DC | Connector:Jack-DC | Connectors:BARREL_JACK | ~ | CP-002A-ND
 |  | J2 | PWR_INV | Connector_Generic:Conn_01x02 | Power Sense PCB:AMASS_XT60-M | ~
 |  | J3 | PWR_INPUT | Connector_Generic:Conn_01x02 | Power Sense PCB:AMASS_XT60-M | ~
 |  | J4 | PHASE_A_INV | Connector_Generic:Conn_01x01 | Power Sense PCB:3mm_Bullet_RA | ~
 |  | J5 | PHASE_A_MOTOR | Connector_Generic:Conn_01x01 | Power Sense PCB:3mm_Bullet_RA | ~
 |  | J6 | PHASE_B_INV | Connector_Generic:Conn_01x01 | Power Sense PCB:3mm_Bullet_RA | ~
 |  | J7 | PHASE_B_MOTOR | Connector_Generic:Conn_01x01 | Power Sense PCB:3mm_Bullet_RA | ~
 |  | J8 | PHASE_C_INV | Connector_Generic:Conn_01x01 | Power Sense PCB:3mm_Bullet_RA | ~
 |  | J9 | PHASE_C_MOTOR | Connector_Generic:Conn_01x01 | Power Sense PCB:3mm_Bullet_RA | ~
 |  | J10 | Test Conn | Connector_Generic:Conn_01x08 | Pin_Headers:Pin_Header_Straight_1x08_Pitch2.54mm | ~ | 961108-6404-AR
 |  | NT1 | Net-Tie_2 | Device:Net-Tie_2 | NetTies:NetTie-2_SMD_Pad0.5mm | ~
 |  | NT2 | Net-Tie_2 | Device:Net-Tie_2 | NetTies:NetTie-2_SMD_Pad0.5mm | ~
 |  | NT3 | Net-Tie_2 | Device:Net-Tie_2 | NetTies:NetTie-2_SMD_Pad0.5mm | ~
 |  | NT4 | Net-Tie_2 | Device:Net-Tie_2 | NetTies:NetTie-2_SMD_Pad0.5mm | ~
 |  | NT5 | Net-Tie_2 | Device:Net-Tie_2 | NetTies:NetTie-2_SMD_Pad0.5mm | ~
 |  | NT6 | Net-Tie_2 | Device:Net-Tie_2 | NetTies:NetTie-2_SMD_Pad0.5mm | ~
 |  | NT7 | Net-Tie_2 | Device:Net-Tie_2 | NetTies:NetTie-2_SMD_Pad0.5mm | ~
 |  | NT8 | Net-Tie_2 | Device:Net-Tie_2 | NetTies:NetTie-2_SMD_Pad0.5mm | ~
 |  | R1 | 4.99k | Device:R_Small_US | Resistors_SMD:R_0603 | ~
 |  | R2 | 4.99k | Device:R_Small_US | Resistors_SMD:R_0603 | ~
 |  | R3 | 5m | Device:R_US | Power Sense PCB:R_2512_Sense | ~ | YAG6124CT-ND
 |  | R4 | 5m | Device:R_US | Power Sense PCB:R_2512_Sense | ~ | YAG6124CT-ND
 |  | R5 | R_Small_US | Device:R_Small_US | Resistors_SMD:R_0603 | ~
 |  | R6 | R_Small_US | Device:R_Small_US | Resistors_SMD:R_0603 | ~
 |  | R7 | 22k | Device:R_Small_US | Resistors_SMD:R_0603 | ~
 |  | R8 | 10k | Device:R_Small_US | Resistors_SMD:R_0603 | ~
 |  | R9 | 10k | Device:R_Small_US | Resistors_SMD:R_0603 | ~
 |  | R10 | 5m | Device:R_US | Power Sense PCB:R_2512_Sense | ~ | YAG6124CT-ND
 |  | R11 | 10k | Device:R_Small_US | Resistors_SMD:R_0603 | ~
 |  | R12 | R_Small_US | Device:R_Small_US | Resistors_SMD:R_0603 | ~
 |  | R13 | 4.99k | Device:R_Small_US | Resistors_SMD:R_0603 | ~
 |  | R14 | 5m | Device:R_US | Power Sense PCB:R_2512_Sense | ~ | YAG6124CT-ND
 |  | R15 | R_Small_US | Device:R_Small_US | Resistors_SMD:R_0603 | ~
 |  | R16 | 22k | Device:R_Small_US | Resistors_SMD:R_0603 | ~
 |  | R17 | 4.99k | Device:R_Small_US | Resistors_SMD:R_0603 | ~
 |  | R18 | 22k | Device:R_Small_US | Resistors_SMD:R_0603 | ~
 |  | R19 | 22k | Device:R_Small_US | Resistors_SMD:R_0603 | ~
 |  | U1 | INA240A1D | Amplifier_Current:INA240A1D | Housings_SOIC:SOIC-8-1EP_3.9x4.9mm_Pitch1.27mm | http://www.ti.com/lit/ds/symlink/ina240.pdf | 296-49646-1-ND
 |  | U2 | INA240A1D | Amplifier_Current:INA240A1D | Housings_SOIC:SOIC-8-1EP_3.9x4.9mm_Pitch1.27mm | http://www.ti.com/lit/ds/symlink/ina240.pdf | 296-49646-1-ND
 |  | U3 | INA240A1D | Amplifier_Current:INA240A1D | Housings_SOIC:SOIC-8-1EP_3.9x4.9mm_Pitch1.27mm | http://www.ti.com/lit/ds/symlink/ina240.pdf | 296-49646-1-ND
 |  | U4 | INA240A1D | Amplifier_Current:INA240A1D | Housings_SOIC:SOIC-8-1EP_3.9x4.9mm_Pitch1.27mm | http://www.ti.com/lit/ds/symlink/ina240.pdf | 296-49646-1-ND
Collated Components:
Item | Qty | Reference(s) | Value | LibPart | Footprint | Datasheet | Digikey
1 | 8 | C1, C2, C7, C10, C13, C14, C15, C16 | 0.1uF | Device:C_Small | Capacitors_SMD:C_0805 | ~ | 478-12799-1-ND
2 | 8 | C3, C4, C5, C6, C8, C9, C11, C12 | C_Small | Device:C_Small | Capacitors_SMD:C_0603 | ~
3 | 4 | H1, H2, H3, H4 | MountingHole | Mechanical:MountingHole | Mounting_Holes:MountingHole_3mm_Pad_Via | ~
4 | 1 | J1 | Jack-DC | Connector:Jack-DC | Connectors:BARREL_JACK | ~ | CP-002A-ND
5 | 1 | J2 | PWR_INV | Connector_Generic:Conn_01x02 | Power Sense PCB:AMASS_XT60-M | ~
6 | 1 | J3 | PWR_INPUT | Connector_Generic:Conn_01x02 | Power Sense PCB:AMASS_XT60-M | ~
7 | 1 | J4 | PHASE_A_INV | Connector_Generic:Conn_01x01 | Power Sense PCB:3mm_Bullet_RA | ~
8 | 1 | J5 | PHASE_A_MOTOR | Connector_Generic:Conn_01x01 | Power Sense PCB:3mm_Bullet_RA | ~
9 | 1 | J6 | PHASE_B_INV | Connector_Generic:Conn_01x01 | Power Sense PCB:3mm_Bullet_RA | ~
10 | 1 | J7 | PHASE_B_MOTOR | Connector_Generic:Conn_01x01 | Power Sense PCB:3mm_Bullet_RA | ~
11 | 1 | J8 | PHASE_C_INV | Connector_Generic:Conn_01x01 | Power Sense PCB:3mm_Bullet_RA | ~
12 | 1 | J9 | PHASE_C_MOTOR | Connector_Generic:Conn_01x01 | Power Sense PCB:3mm_Bullet_RA | ~
13 | 1 | J10 | Test Conn | Connector_Generic:Conn_01x08 | Pin_Headers:Pin_Header_Straight_1x08_Pitch2.54mm | ~ | 961108-6404-AR
14 | 8 | NT1, NT2, NT3, NT4, NT5, NT6, NT7, NT8 | Net-Tie_2 | Device:Net-Tie_2 | NetTies:NetTie-2_SMD_Pad0.5mm | ~
15 | 4 | R1, R2, R13, R17 | 4.99k | Device:R_Small_US | Resistors_SMD:R_0603 | ~
16 | 4 | R3, R4, R10, R14 | 5m | Device:R_US | Power Sense PCB:R_2512_Sense | ~ | YAG6124CT-ND
17 | 4 | R5, R6, R12, R15 | R_Small_US | Device:R_Small_US | Resistors_SMD:R_0603 | ~
18 | 4 | R7, R16, R18, R19 | 22k | Device:R_Small_US | Resistors_SMD:R_0603 | ~
19 | 3 | R8, R9, R11 | 10k | Device:R_Small_US | Resistors_SMD:R_0603 | ~
20 | 4 | U1, U2, U3, U4 | INA240A1D | Amplifier_Current:INA240A1D | Housings_SOIC:SOIC-8-1EP_3.9x4.9mm_Pitch1.27mm | http://www.ti.com/lit/ds/symlink/ina240.pdf | 296-49646-1-ND

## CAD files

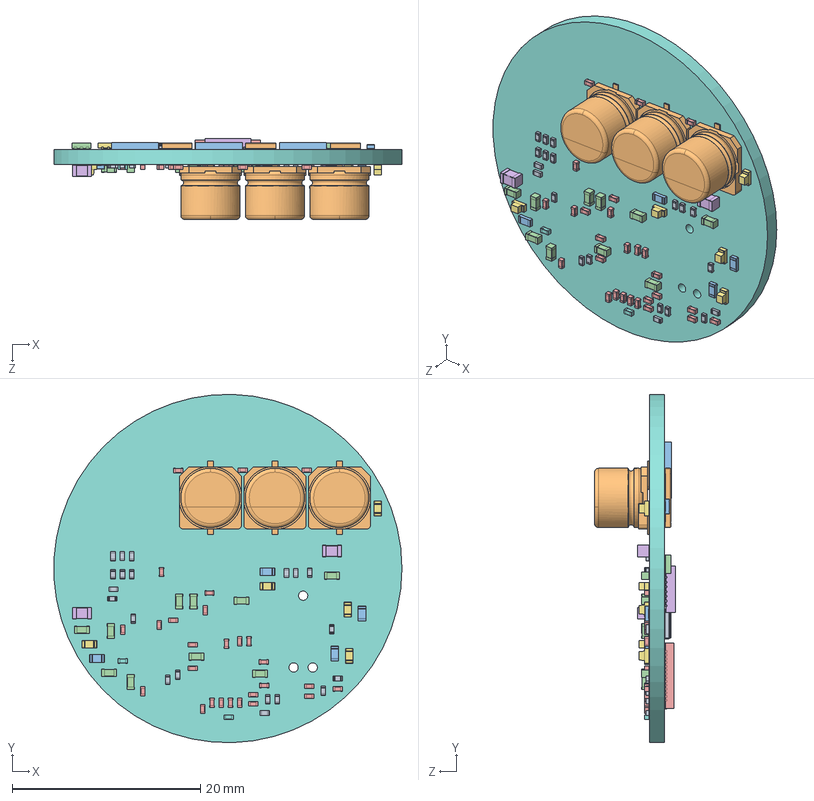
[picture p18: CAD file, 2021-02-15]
hardware/Thruster_Controller_V2/PCB 3D Model/Thruster_Controller_V2.1.step.SLDASM
37.0 x 37.0 x 8.60 mm
SOLID.step
SOLID-0.step x 3
SOLID-1.step x 3
SOLID-2.step x 10
SOLID-3.step x 29
SOLID-4.step x 2
SOLID-5.step x 5
SOLID-6.step x 2
SOLID-7.step x 27
SOLID-8.step x 3
SOLID-9.step x 5
SOLID-10.step x 2
SOLID-11.step
SOLID-12.step
SOLID-13.step
COMPOUND.step

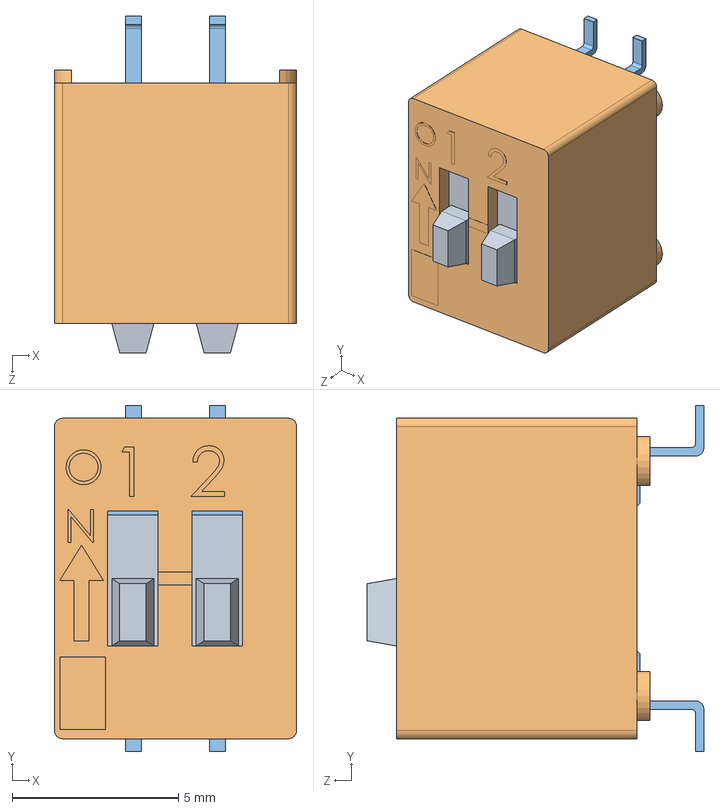
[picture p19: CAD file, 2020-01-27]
hardware/XDS100v2 Programmer/3D Models/204-2 (1).SLDASM
7.29 x 10.4 x 10.1 mm
206-56-014-35-01.stp x 2
204-40-038(for 204008).stp
204-93&94-8pole.stp

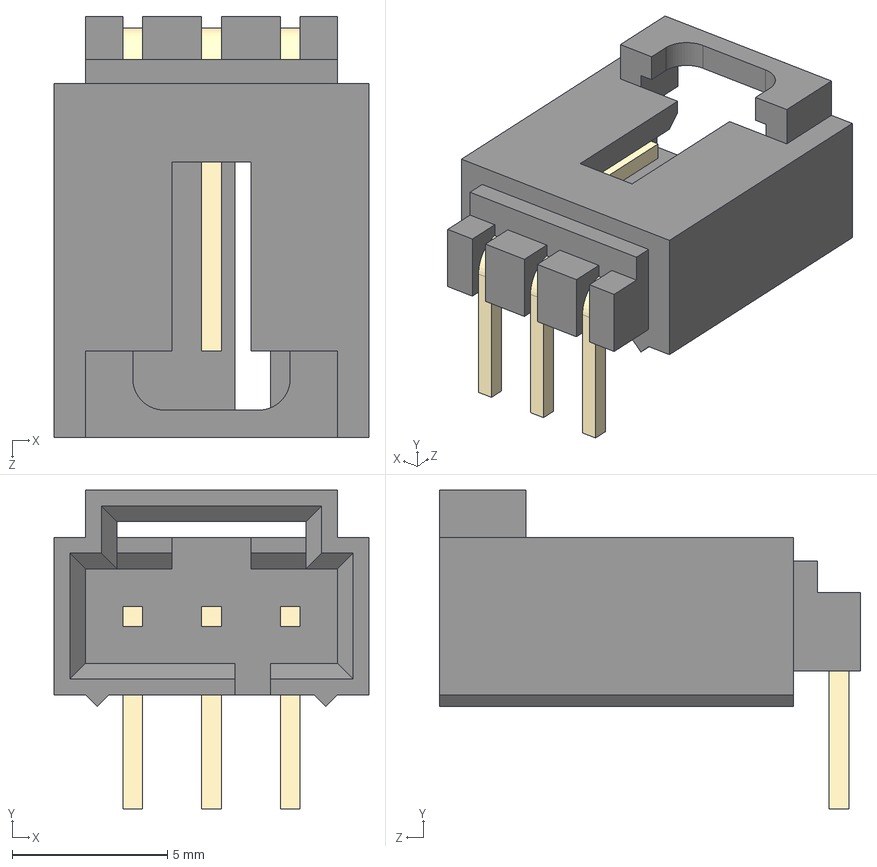
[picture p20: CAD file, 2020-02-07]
hardware/MCU_Powertrain/3D Models/3pinRA.STEP
10.2 x 10.3 x 13.6 mm

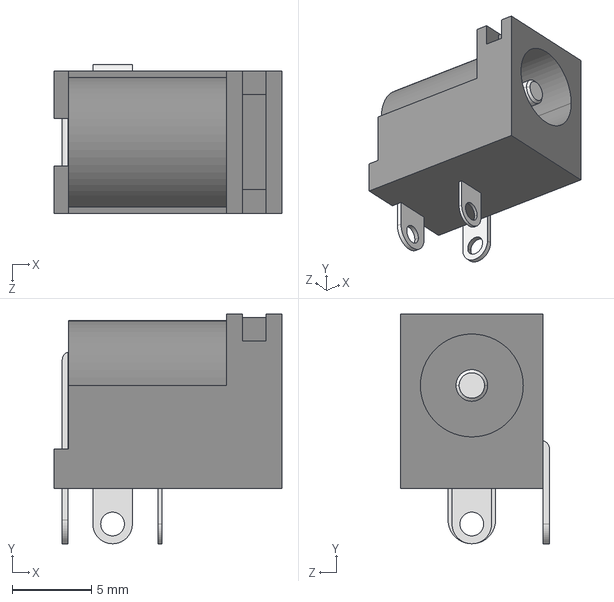
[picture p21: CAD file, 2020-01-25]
hardware/Power Sense PCB/3D Models/CUI_DEVICES_PJ-002A.step
14.4 x 14.5 x 9.40 mm

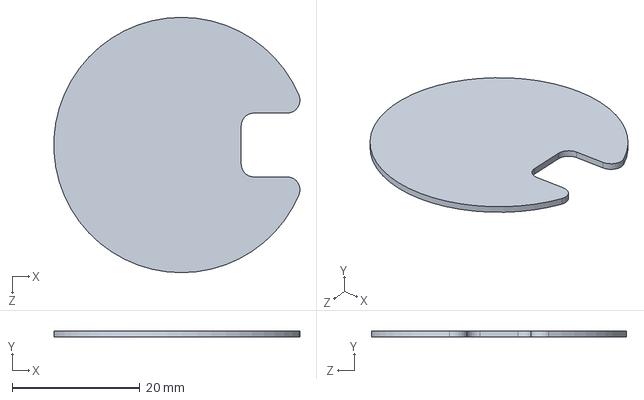
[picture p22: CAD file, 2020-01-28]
hardware/RPM Sensor/Outline.SLDPRT
38.5 x 1.00 x 40.0 mm

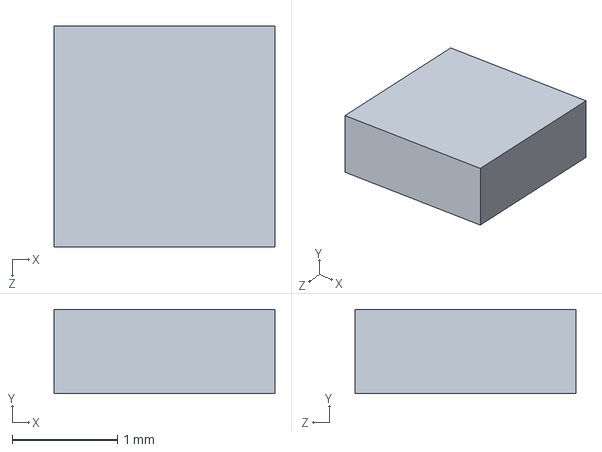
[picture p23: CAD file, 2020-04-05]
hardware/Thruster_Controller_V2/3D Models/2x2_chip.SLDPRT
2.10 x 0.8 x 2.10 mm

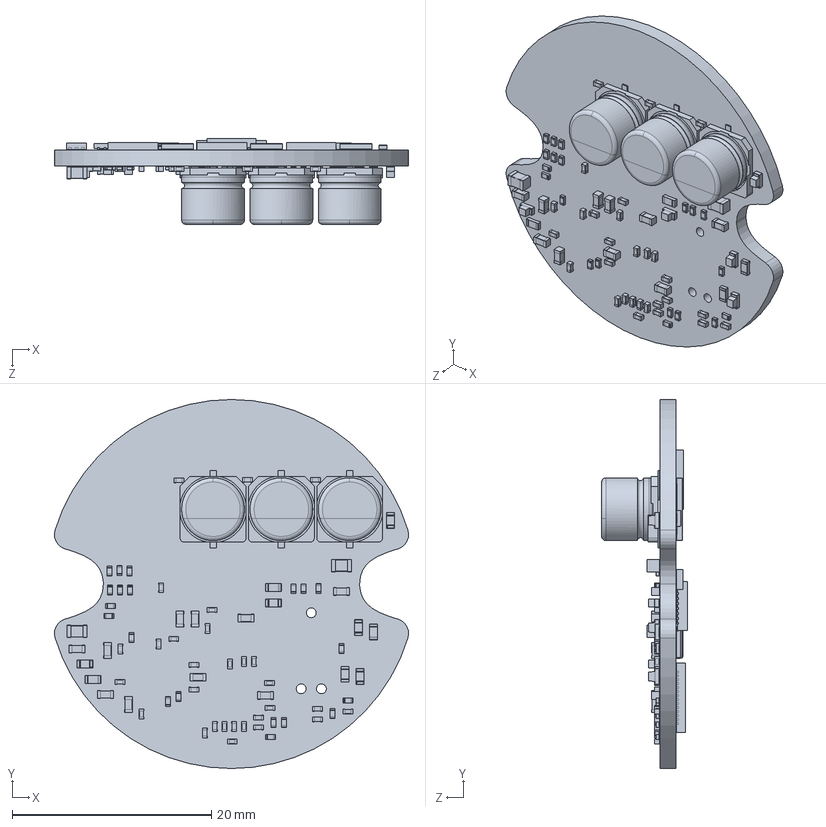
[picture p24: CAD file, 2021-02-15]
hardware/Thruster_Controller_V2/PCB 3D Model/Thruster_Controller_V2.1.SLDPRT
35.5 x 37.0 x 8.60 mm

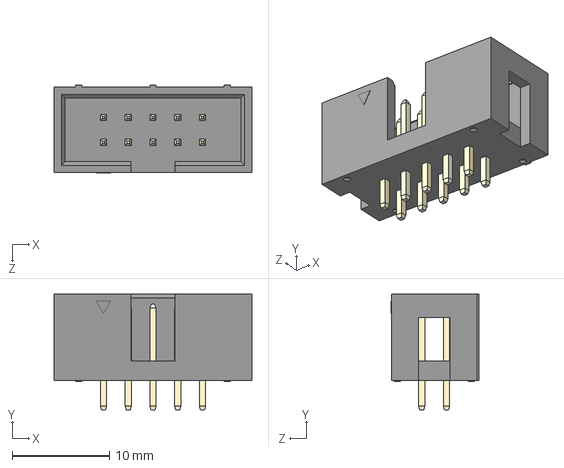
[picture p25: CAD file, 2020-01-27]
hardware/XDS100v2 Programmer/3D Models/3020-10-0100-xx.STEP
20.3 x 11.9 x 9.03 mm

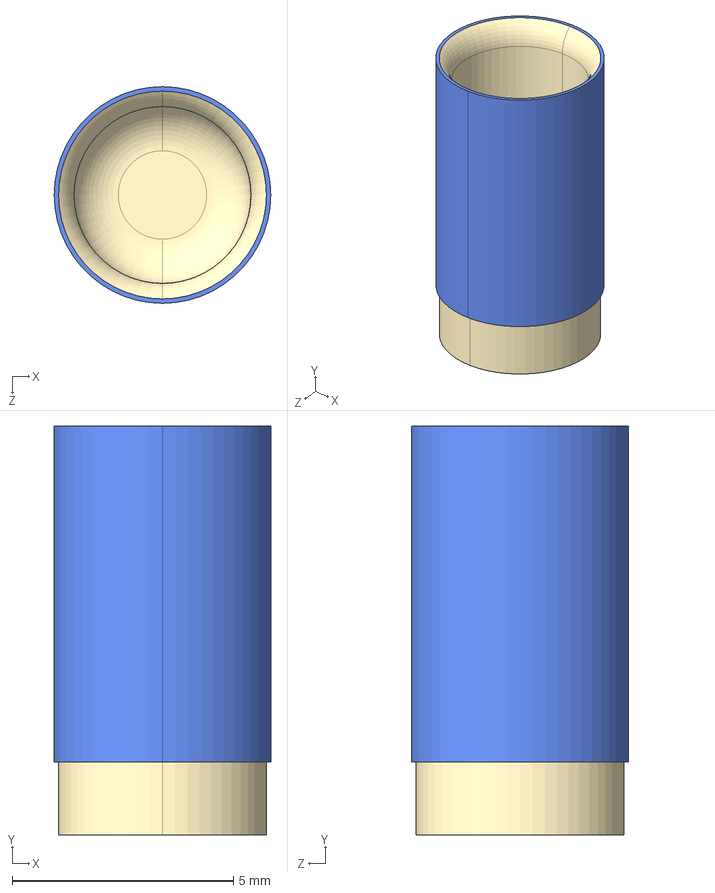
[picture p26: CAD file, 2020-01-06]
hardware/Power Sense PCB/3D Models/BulletC.STEP
4.90 x 9.25 x 4.90 mm

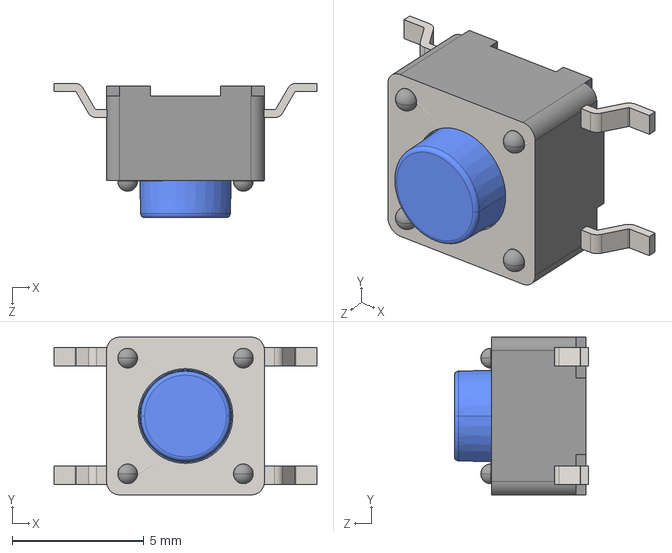
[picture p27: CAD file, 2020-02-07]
hardware/Thruster_Controller_V2/3D Models/TL3301AFxxxxG (1).STEP
10.0 x 6.00 x 5.10 mm
Body1.stp
Body2.stp

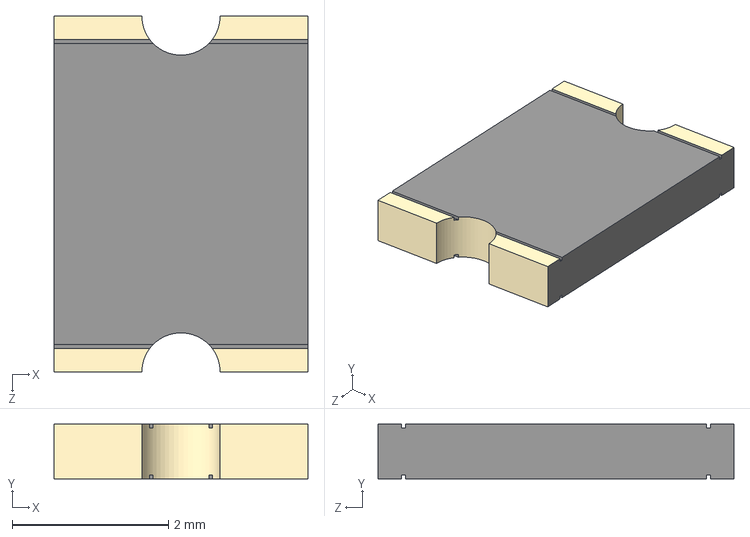
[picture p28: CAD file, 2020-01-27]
hardware/XDS100v2 Programmer/3D Models/Fuse.STEP
3.24 x 0.7 x 4.55 mm

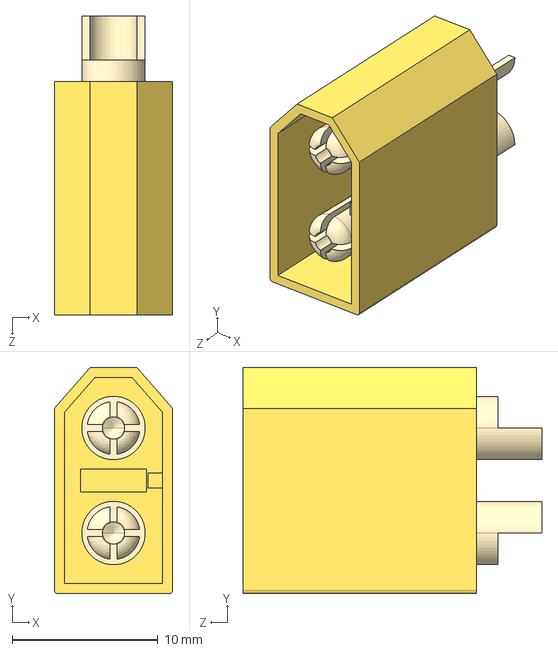
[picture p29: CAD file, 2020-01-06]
hardware/Power Sense PCB/3D Models/XT60.STEP
8.10 x 15.5 x 20.5 mm

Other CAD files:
hardware/XDS100v2 Programmer/3D Models/204-3.SLDASM
firmware/can_ex3_external_transmit/CPU1_RAM/can_ex3_external_transmit.obj
firmware/can_ex3_external_transmit/CPU1_RAM/device/device.obj
hardware/XDS100v2 Programmer/3D Models/204-2.STEP
firmware/can_ex3_external_transmit/CPU1_RAM/device/f28004x_codestartbranch.obj
hardware/MCU_Powertrain/3D Models/3020-10-0100-xx.SLDPRT
hardware/MCU_Powertrain/3D Models/3020-10-0100-xx.igs
hardware/MCU_Powertrain/3D Models/5x6mm FET.SLDPRT
hardware/MCU_Powertrain/3D Models/5x6mm FET.STEP
hardware/MCU_Powertrain/3D Models/705530002.SLDPRT
hardware/MCU_Powertrain/3D Models/705530002.STEP
hardware/MCU_Powertrain/3D Models/BulletA.SLDPRT
hardware/MCU_Powertrain/3D Models/BulletA.STEP
hardware/MCU_Powertrain/3D Models/BulletB.SLDPRT
hardware/MCU_Powertrain/3D Models/BulletB.STEP
hardware/MCU_Powertrain/3D Models/BulletC.SLDPRT
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

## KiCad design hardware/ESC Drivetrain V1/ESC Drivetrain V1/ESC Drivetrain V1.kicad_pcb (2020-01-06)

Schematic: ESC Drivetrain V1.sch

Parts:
C1: 4.7uF; C_0603; Digikey 1276-1900-1-ND
C2, C4: 0.047uF; C_0603; Digikey 399-7933-1-ND
C3, C5, C20, C27: 1uF; C_0603; Digikey 1276-1102-1-ND
C6, C7, C8, C17, C23: 0.1uF; C_0603; Digikey 1276-CL10B104KB8NNNLCT-ND
C9, C16, C18: 1000pF; C_0603; Digikey 1276-1018-1-ND
C10, C11, C12: 220uF; CP_Elec_8x10.5; Digikey 25PEV220M8X10.5CT-ND
C13, C14, C15, C21: 22uF; C_0805; Digikey 490-14661-1-ND
C19: 2.2uF; C_0603; Digikey 490-10731-1-ND
C22: 0.33uF; C_0603; Digikey 1276-2370-1-ND
C24, C25, C26: 2200pF; C_0603; Digikey 490-1459-1-ND
D1: BLUE; LED_0603; Digikey 160-1827-1-ND
D2: RED; LED_0603; Digikey 160-1447-1-ND
D3: GREEN; LED_0603; Digikey 160-1446-1-ND
D4: D_Schottky_ALT; D_SOD-123F; Digikey MBR1H100SFT3GOSCT-ND
J1: PHASE_A; 3mm_Bullet_A
J2: Conn_01x02; AMASS_XT60-M
J3: PHASE_B; 3mm_Bullet_B
J4: PHASE_C; 3mm_Bullet_C
J5, J6: Conn_02x10_Odd_Even; Pin_Header_Straight_2x10_Pitch2.54mm_LaunchPad
J7: I2C Header; Pin_Header_Straight_1x03_Pitch2.54mm
L1: 15uH; Eaton_Inductor; Digikey 513-1458-1-ND
Q1, Q2, Q3: SIZF906DT; Digikey SIZF906DT-T1-GE3CT-ND
R1, R6: 10kΩ; R_0603; Digikey RNCP0603FTD10K0CT-ND
R2: 100Ω; R_0603; Digikey RHM100DCT-ND
R3, R4, R5, R15: 22.0kΩ; R_0603; Digikey P22KDBCT-ND
R7, R23, R24: 2.7kΩ; R_0603; Digikey P2.7KDACT-ND
R8, R9, R11: 5mΩ; R_2512_Sense; Digikey YAG6124CT-ND
R10: 330Ω; R_0603; Digikey RHM330DCT-ND
R12, R13, R14, R16: 4.99kΩ; R_0603; Digikey P4.99KDBCT-ND
R17: 330Ω; R_0603
R18: 68.0kΩ; R_0603; Digikey P68KDBCT-ND
R19: 20.0kΩ; R_0603; Digikey P20KDBCT-ND
R20, R21, R22: 56Ω; R_0603; Digikey A129673CT-ND
U1: DRV8305; Digikey 296-42659-1-ND
U2: LMR16006XDDC; SOT-23-6; Digikey 296-40293-1-ND
U3: SRV05-4; SOT-23-6; Digikey SRV05-4CT-ND

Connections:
+3V3: C21.2, C27.1, D2.2 (A), D3.2 (A), J5.2, L1.2, R1.1, R6.1, R18.1, R23.1, R24.1, U1.48, U3.5
+12V: C1.1, C10.1, C11.1, C12.1, C13.2, C14.2, C15.2, C19.1, C23.1, D1.2 (A), J2.2, Q1.4, Q2.4, Q3.4, R2.1, R15.1, U1.41, U2.5
/ADC_IN: J5.20
/EN_GATE: J6.15, U1.1
/GH_A: Q3.1, U1.36
/GH_B: Q1.1, U1.29
/GH_C: Q2.1, U1.28
/GL_A: Q3.3, U1.33
/GL_B: Q1.3, U1.32
/GL_C: Q2.3, U1.25
/INH_A: J6.2, U1.2
/INH_B: J6.6, U1.4
/INH_C: J6.10, U1.6
/INL_A: J6.4, U1.3
/INL_B: J6.8, U1.5
/INL_C: J6.12, U1.7
/ISEN_A: R20.1, U1.16
/ISEN_B: R21.1, U1.17
/ISEN_C: R22.1, U1.18
/PHASE_A: J1.1, Q3.5, R5.1
/PHASE_B: J3.1, Q1.5, R3.1
/PHASE_C: J4.1, Q2.5, R4.1
/PWRGD: J6.9, R1.2, U1.13
/SCLK: J5.14, U1.12
/SCL_EXTERN: J6.16, J7.2, R24.2
/SCS: J6.3, U1.9
/SDA_EXTERN: J6.14, J7.3, R23.2
/SDI: J6.11, U1.10
/SDO: J6.13, U1.11
/SH_A: Q3.2, U1.35
/SH_B: Q1.2, U1.30
/SH_C: Q2.2, U1.27
/SL_A: C9.1, Q3.6, R11.1, U1.23, U1.34
/SL_B: C16.1, Q1.6, R8.1, U1.21, U1.31
/SL_C: C18.1, Q2.6, R9.1, U1.19, U1.26
/VSEN_A: C8.1, J5.5, R5.2, R14.1, U3.3
/VSEN_B: C6.1, J5.7, R3.2, R12.1, U3.6
/VSEN_C: C7.1, J5.9, R4.2, R13.1, U3.4
/VSEN_PVDD: C17.1, J5.11, R15.2, R16.1, U3.1
/WAKE: J6.17, U1.47
/nFAULT: J5.6, R6.2, R10.2, U1.8
GND: C1.2, C3.2, C5.2, C6.2, C7.2, C8.2, C9.2, C10.2, C11.2, C12.2, C13.1, C14.1, C15.1, C16.2, C17.2, C18.2, C20.2, C21.1, C23.2, C24.2, C25.2, C26.2, C27.2, D4.2 (A), J2.1, J5.3, J6.1, J7.1, R7.2, R8.2, R9.2, R11.2, R12.2, R13.2, R14.2, R16.2, R17.2, R19.2, U1.14, U1.20, U1.22, U1.24, U1.45, U1.49, U2.2, U3.2
unnamed: C2.1, U1.42
unnamed: C2.2, U1.43
unnamed: C3.1, U1.15
unnamed: C4.1, U1.40
unnamed: C4.2, U1.39
unnamed: C5.1, U1.46
unnamed: C19.2, U1.38
unnamed: C20.1, U1.37
unnamed: C22.1, D4.1 (K), L1.1, U2.6
unnamed: C22.2, U2.1
unnamed: C24.1, J5.13, R20.2
unnamed: C25.1, J5.15, R21.2
unnamed: C26.1, J5.17, R22.2
unnamed: D1.1 (K), R7.1
unnamed: D2.1 (K), R10.1
unnamed: D3.1 (K), R17.1
unnamed: R2.2, U1.44
unnamed: R18.2, R19.1, U2.3

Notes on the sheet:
FOC ESC Drivetrain V1
Mark Belbin -- Aug 2019
Aluminum Polymer Bulk Capacitance
Ceramic High Frequency Decoupling
H-Bridges and VIN
3.3V Regulator
Headers and Protection
DRV8305
SDA = SDAA, GPIO 32
SCL = SCLA, GPIO 33
Optional Pullup Resistors

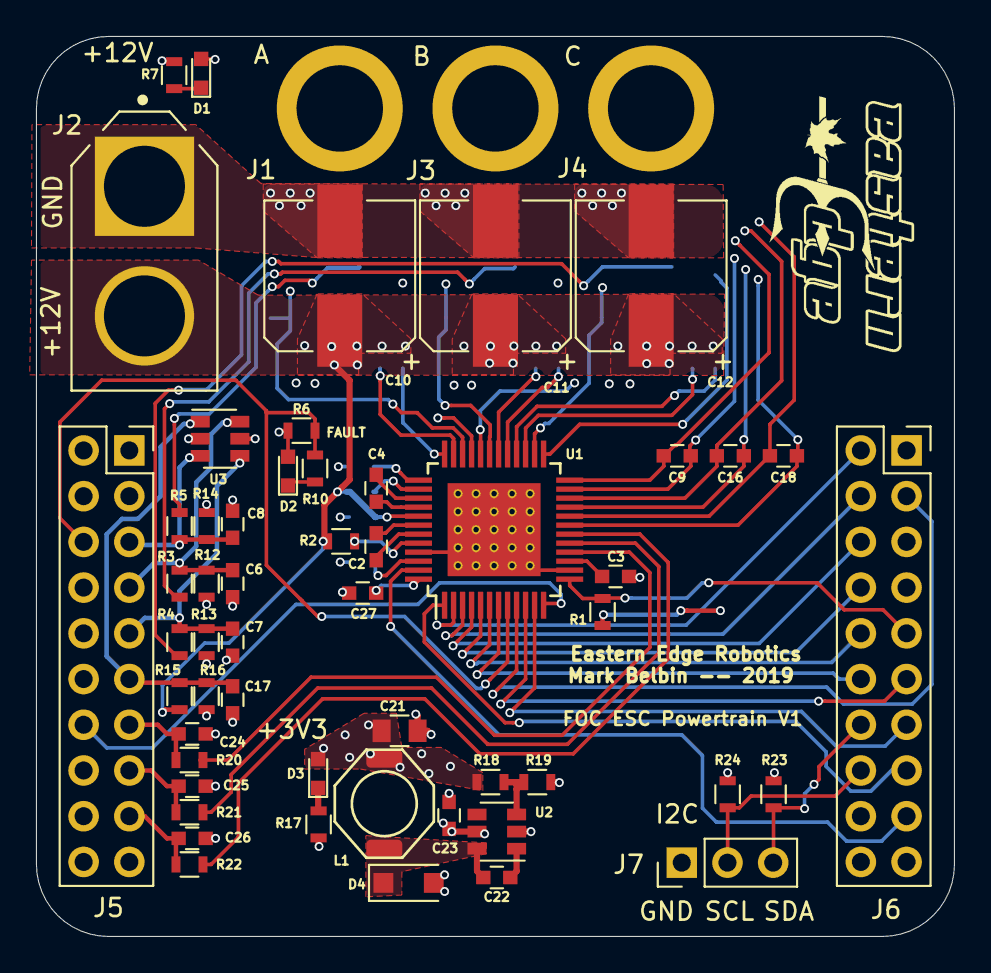
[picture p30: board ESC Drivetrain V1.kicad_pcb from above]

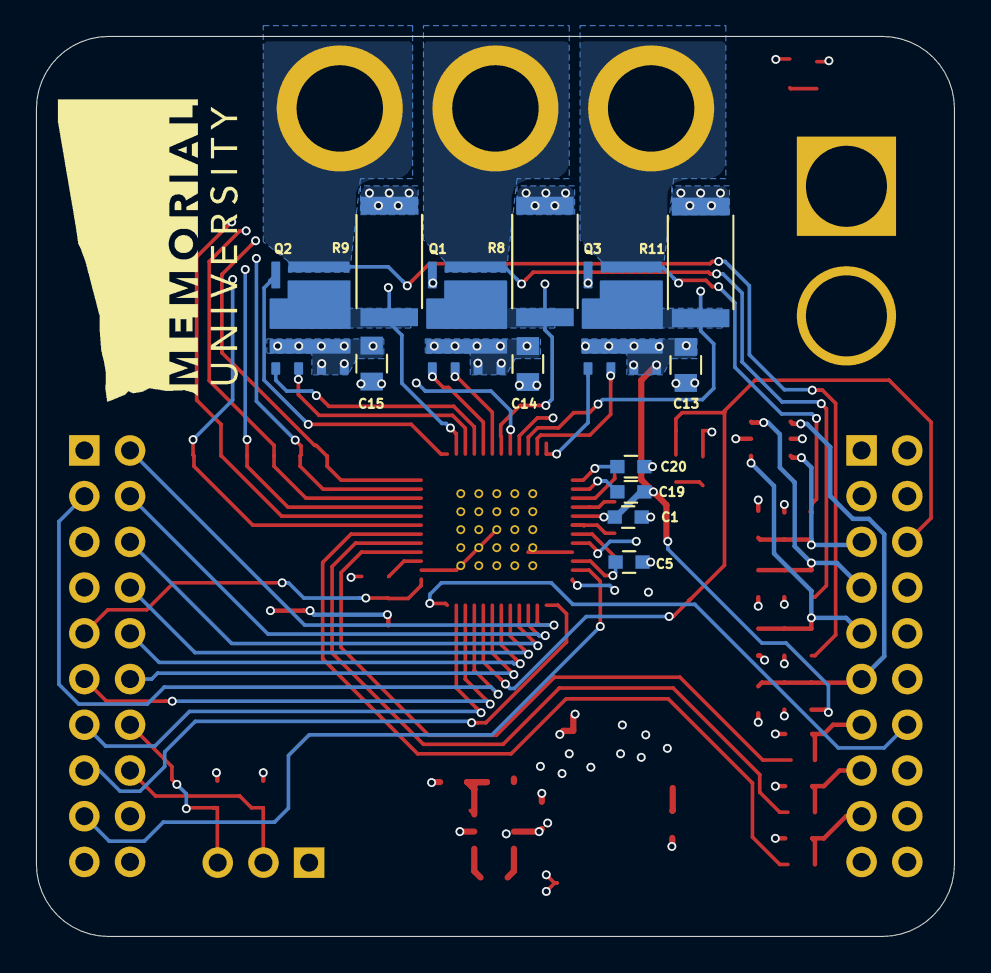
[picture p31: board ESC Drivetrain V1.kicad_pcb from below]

Board: 4 copper layers, 51.0 x 50.0 mm, 71 parts (14 on the bottom side), 59 nets.

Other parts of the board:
U$12: EERLOGO
U$15: MUNLOGO

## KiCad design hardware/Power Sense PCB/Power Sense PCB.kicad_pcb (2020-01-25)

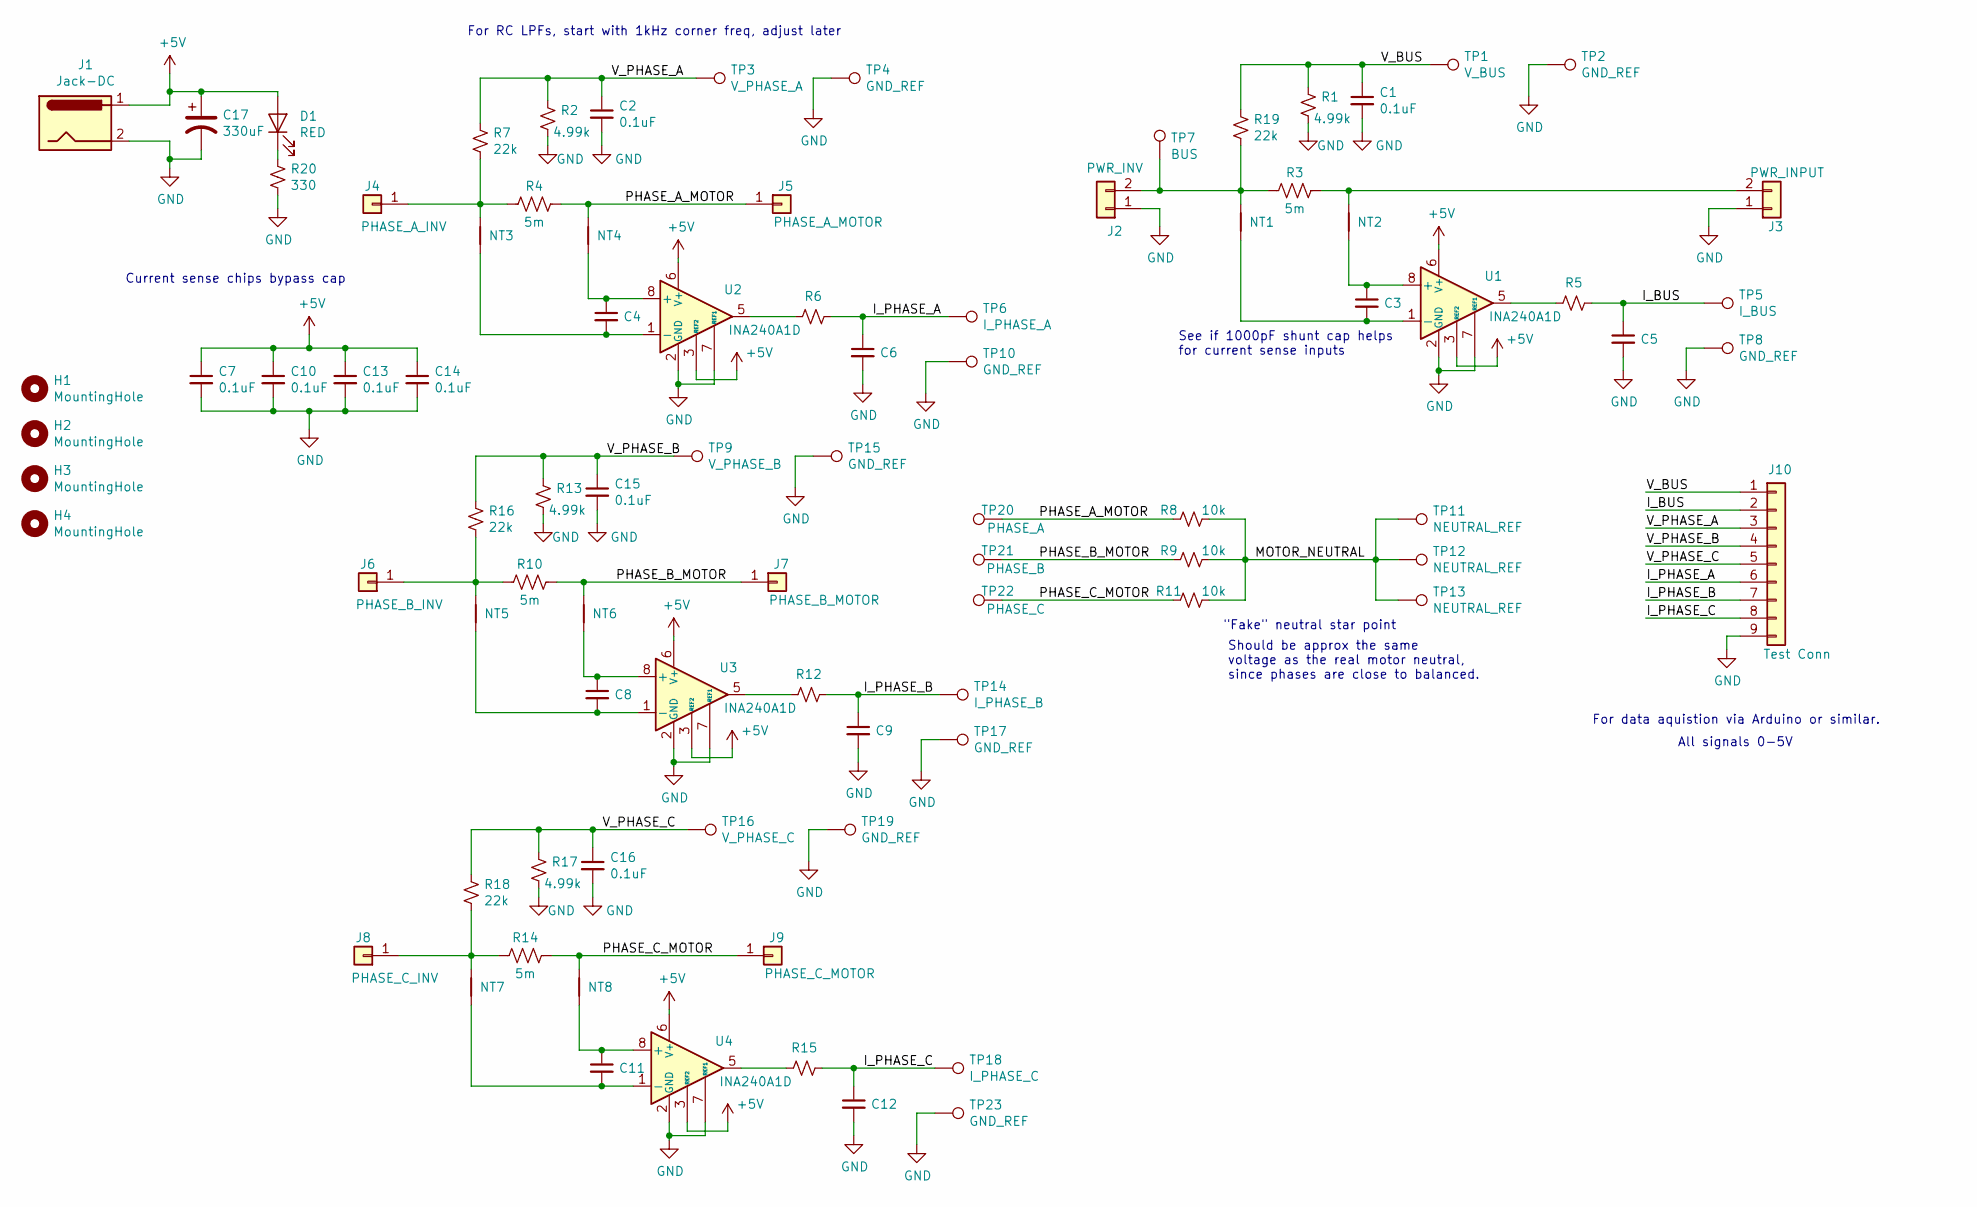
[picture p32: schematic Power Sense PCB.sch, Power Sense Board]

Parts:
C1, C2, C7, C10, C13, C14, C15, C16: 0.1uF; C_0805; Digikey 478-12799-1-ND
C3, C4, C5, C6, C8, C9, C11, C12: C_Small; C_0603
C17: 330uF; CP_Radial_D8.0mm_P3.50mm; Digikey 493-15427-ND
D1: RED; LED_0603; Digikey 160-1447-1-ND
H1, H2, H3, H4: MountingHole; MountingHole_3mm_Pad_Via
J1: Jack-DC; BARREL_JACK; Digikey CP-002A-ND
J2: PWR_INV; AMASS_XT60-M
J3: PWR_INPUT; AMASS_XT60-M
J4: PHASE_A_INV; 3mm_Bullet_RA
J5: PHASE_A_MOTOR; 3mm_Bullet_RA
J6: PHASE_B_INV; 3mm_Bullet_RA
J7: PHASE_B_MOTOR; 3mm_Bullet_RA
J8: PHASE_C_INV; 3mm_Bullet_RA
J9: PHASE_C_MOTOR; 3mm_Bullet_RA
J10: Test Conn; Pin_Header_Straight_1x09_Pitch2.54mm; Digikey 3M9457-09-ND
NT1, NT2, NT3, NT4, NT5, NT6, NT7, NT8: Net-Tie_2; NetTie-2_SMD_Pad0.25mm
R1, R2, R13, R17: 4.99k; R_0603; Digikey P4.99KDBCT-ND
R3, R4, R10, R14: 5m; R_2512_Sense; Digikey YAG6124CT-ND
R5, R6, R12, R15: R_Small_US; R_0603
R7, R16, R18, R19: 22k; R_0603; Digikey P22KDBCT-ND
R8, R9, R11: 10k; R_0603
R20: 330; R_0603; Digikey RHM330DCT-ND
TP1: V_BUS; TestPoint_Loop_D1.80mm_Drill1.0mm_Beaded; Digikey 36-5117-ND
TP2, TP4, TP8, TP10, TP15, TP17, TP19, TP23: GND_REF; TestPoint_Loop_D1.80mm_Drill1.0mm_Beaded; Digikey 36-5001-ND
TP3: V_PHASE_A; TestPoint_Loop_D1.80mm_Drill1.0mm_Beaded; Digikey 36-5117-ND
TP5: I_BUS; TestPoint_Loop_D1.80mm_Drill1.0mm_Beaded; Digikey 36-5119-ND
TP6: I_PHASE_A; TestPoint_Loop_D1.80mm_Drill1.0mm_Beaded; Digikey 36-5119-ND
TP7: BUS; TestPoint_Loop_D1.80mm_Drill1.0mm_Beaded; Digikey 36-5116-ND
TP9: V_PHASE_B; TestPoint_Loop_D1.80mm_Drill1.0mm_Beaded; Digikey 36-5117-ND
TP11, TP12, TP13: NEUTRAL_REF; TestPoint_Loop_D1.80mm_Drill1.0mm_Beaded; Digikey 36-5001-ND
TP14: I_PHASE_B; TestPoint_Loop_D1.80mm_Drill1.0mm_Beaded; Digikey 36-5119-ND
TP16: V_PHASE_C; TestPoint_Loop_D1.80mm_Drill1.0mm_Beaded; Digikey 36-5117-ND
TP18: I_PHASE_C; TestPoint_Loop_D1.80mm_Drill1.0mm_Beaded; Digikey 36-5119-ND
TP20: PHASE_A; TestPoint_Loop_D1.80mm_Drill1.0mm_Beaded; Digikey 36-5116-ND
TP21: PHASE_B; TestPoint_Loop_D1.80mm_Drill1.0mm_Beaded; Digikey 36-5116-ND
TP22: PHASE_C; TestPoint_Loop_D1.80mm_Drill1.0mm_Beaded; Digikey 36-5116-ND
U1, U2, U3, U4: INA240A1D; SOIC-8_3.9x4.9mm_Pitch1.27mm; Digikey 296-49646-1-ND

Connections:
+5V: C7.1, C10.1, C13.1, C14.1, C17.1, D1.2 (A), J1.1, U1.3 (REF2), U1.6 (V+), U2.3 (REF2), U2.6 (V+), U3.3 (REF2), U3.6 (V+), U4.3 (REF2), U4.6 (V+)
/I_BUS: C5.1, J10.2, R5.1, TP5.1
/I_PHASE_A: C6.1, J10.6, R6.1, TP6.1
/I_PHASE_B: C9.1, J10.7, R12.1, TP14.1
/I_PHASE_C: C12.1, J10.8, R15.1, TP18.1
/MOTOR_NEUTRAL: R8.1, R9.1, R11.1, TP11.1, TP12.1, TP13.1
/PHASE_A_MOTOR: J5.1, NT4.1, R4.1, R8.2, TP20.1
/PHASE_B_MOTOR: J7.1, NT6.1, R9.2, R10.1, TP21.1
/PHASE_C_MOTOR: J9.1, NT8.1, R11.2, R14.1, TP22.1
/V_BUS: C1.1, J10.1, R1.2, R19.2, TP1.1
/V_PHASE_A: C2.1, J10.3, R2.2, R7.2, TP3.1
/V_PHASE_B: C15.1, J10.4, R13.2, R16.2, TP9.1
/V_PHASE_C: C16.1, J10.5, R17.2, R18.2, TP16.1
GND: C1.2, C2.2, C5.2, C6.2, C7.2, C9.2, C10.2, C12.2, C13.2, C14.2, C15.2, C16.2, C17.2, J1.2, J1.3, J2.1, J3.1, J10.9, R1.1, R2.1, R13.1, R17.1, R20.2, TP2.1, TP4.1, TP8.1, TP10.1, TP15.1, TP17.1, TP19.1, TP23.1, U1.2 (GND), U1.4 (GND), U1.7 (REF1), U2.2 (GND), U2.4 (GND), U2.7 (REF1), U3.2 (GND), U3.4 (GND), U3.7 (REF1), U4.2 (GND), U4.4 (GND), U4.7 (REF1)
unnamed: C3.1, NT2.2, U1.8 (+)
unnamed: C3.2, NT1.2, U1.1 (-)
unnamed: C4.1, NT4.2, U2.8 (+)
unnamed: C4.2, NT3.2, U2.1 (-)
unnamed: C8.1, NT6.2, U3.8 (+)
unnamed: C8.2, NT5.2, U3.1 (-)
unnamed: C11.1, NT8.2, U4.8 (+)
unnamed: C11.2, NT7.2, U4.1 (-)
unnamed: D1.1 (K), R20.1
unnamed: J2.2, NT1.1, R3.2, R19.1, TP7.1
unnamed: J3.2, NT2.1, R3.1
unnamed: J4.1, NT3.1, R4.2, R7.1
unnamed: J6.1, NT5.1, R10.2, R16.1
unnamed: J8.1, NT7.1, R14.2, R18.1
unnamed: R5.2, U1.5
unnamed: R6.2, U2.5
unnamed: R12.2, U3.5
unnamed: R15.2, U4.5

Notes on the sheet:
For RC LPFs, start with 1kHz corner freq, adjust later
See if 1000pF shunt cap helps for current sense inputs
"Fake" neutral star point
Should be approx the same voltage as the real motor neutral, since phases are close to balanced.
Current sense chips bypass cap
For data aquistion via Arduino or similar.
All signals 0-5V

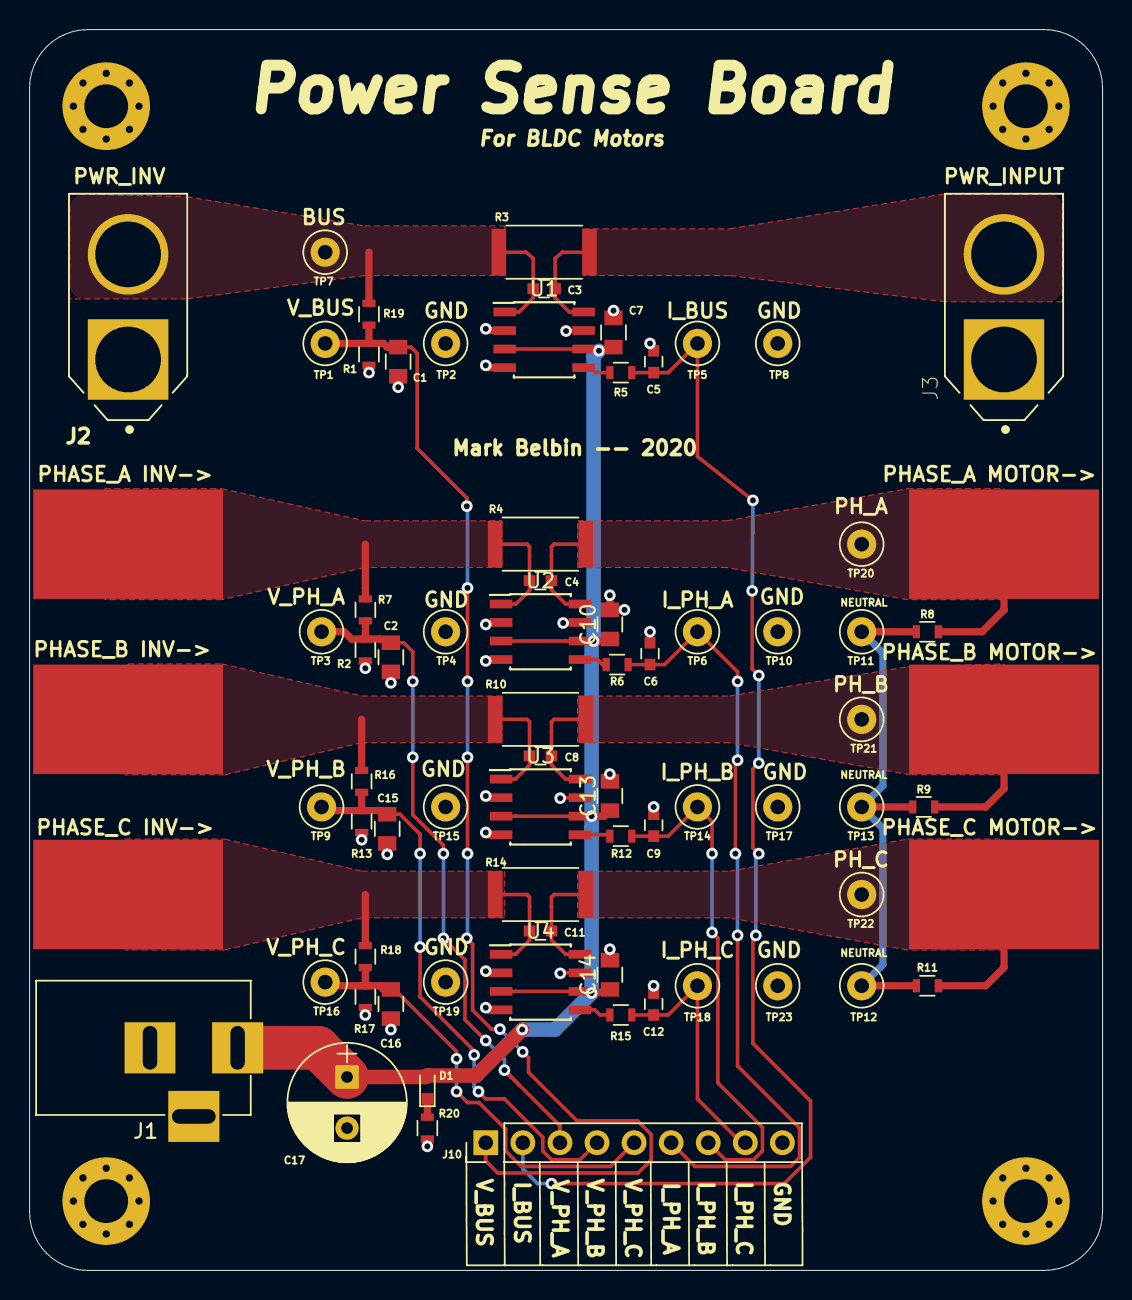
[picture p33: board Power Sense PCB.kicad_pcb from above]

Board: 2 copper layers, 73.5 x 85.0 mm, 87 parts (0 on the bottom side), 32 nets.

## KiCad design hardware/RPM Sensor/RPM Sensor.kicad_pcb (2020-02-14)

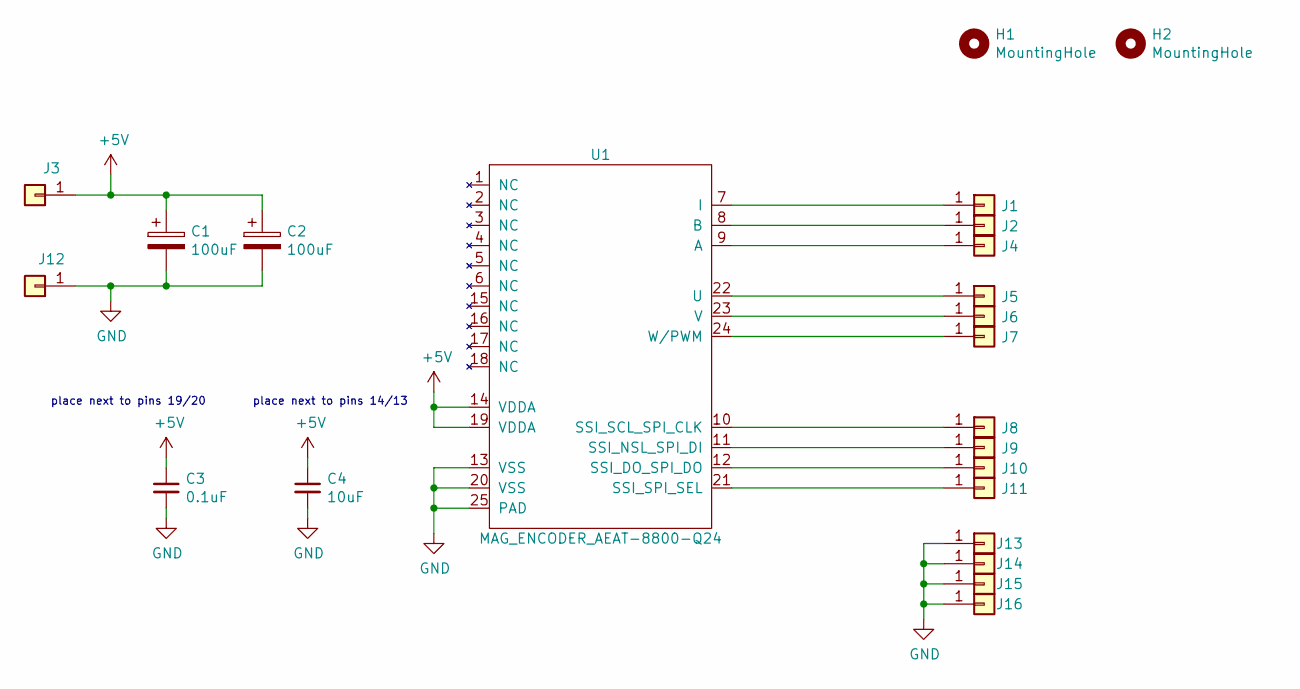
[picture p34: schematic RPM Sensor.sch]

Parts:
C1, C2: 100uF; CP_Tantalum_Case-U_EIA-6032-15_Reflow; Digikey 478-7995-1-ND
C3: 0.1uF; C_0805; Digikey 311-1361-1-ND
C4: 10uF; C_0805; Digikey 399-4925-1-ND
H1, H2: MountingHole; MountingHole_3.2mm_M3_ISO14580
J1, J3, J12, J13, J14, J15, J16: I; TestPoint_Pad_D2.0mm
J2: B; TestPoint_Pad_D2.0mm
J4: A; TestPoint_Pad_D2.0mm
J5: U; TestPoint_Pad_D2.0mm
J6: V; TestPoint_Pad_D2.0mm
J7: W/PWM; TestPoint_Pad_D2.0mm
J8: SCL/CLK; TestPoint_Pad_D2.0mm
J9: NSL/DI; TestPoint_Pad_D2.0mm
J10: DO/DO; TestPoint_Pad_D2.0mm
J11: SEL/SEL; TestPoint_Pad_D2.0mm
U1: MAG_ENCODER_AEAT-8800-Q24; QFN-24-1EP_5x5mm_Pitch0.65mm; Digikey 516-3787-ND

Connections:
+5V: C1.1, C2.1, C3.1, C4.1, J3.1, U1.14 (VDDA), U1.19 (VDDA)
GND: C1.2, C2.2, C3.2, C4.2, J12.1, J13.1, J14.1, J15.1, J16.1, U1.13 (VSS), U1.20 (VSS), U1.25 (PAD)
unnamed: J1.1, U1.7 (I)
unnamed: J2.1, U1.8 (B)
unnamed: J4.1, U1.9 (A)
unnamed: J5.1, U1.22 (U)
unnamed: J6.1, U1.23 (V)
unnamed: J7.1, U1.24 (W/PWM)
unnamed: J8.1, U1.10 (SSI_SCL_SPI_CLK)
unnamed: J9.1, U1.11 (SSI_NSL_SPI_DI)
unnamed: J10.1, U1.12 (SSI_DO_SPI_DO)
unnamed: J11.1, U1.21 (SSI_SPI_SEL)

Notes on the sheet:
place next to pins 14/13
place next to pins 19/20

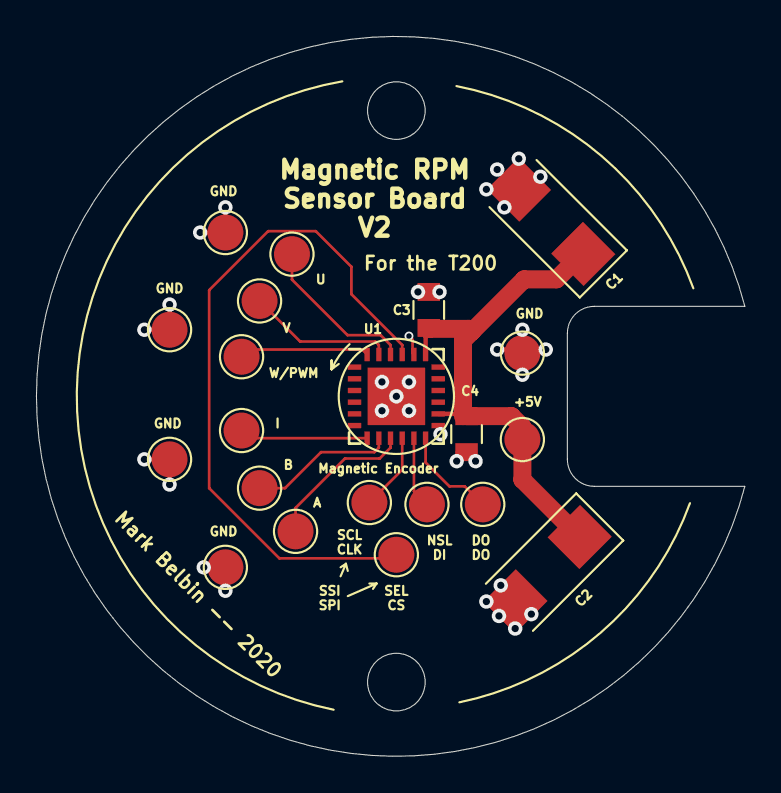
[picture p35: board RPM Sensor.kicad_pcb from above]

Board: 2 copper layers, 39.4 x 40.0 mm, 23 parts (0 on the bottom side), 12 nets.

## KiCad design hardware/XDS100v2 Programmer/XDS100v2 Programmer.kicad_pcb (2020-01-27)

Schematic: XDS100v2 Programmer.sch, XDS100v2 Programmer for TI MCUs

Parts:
C1, C2: 4.7uF; C_0805; Digikey 490-14466-1-ND
C3: 1uF; C_0805; Digikey 399-8011-1-ND
C4: 100uF; CP_Tantalum_Case-U_EIA-6032-15_Reflow; Digikey 478-7995-1-ND
C5, C6, C7, C8, C10, C11: 0.1uF; C_0805; Digikey 311-1361-1-ND
C9: 3.3uF; C_0805; Digikey 490-13309-1-ND
C12, C13: 36p; C_0603; Digikey 490-1416-1-ND
D1: LED; LED_0805; Digikey 475-1278-1-ND
D2, D3: LED; LED_0805; Digikey 160-1579-1-ND‎
F1: 500mA; 1812_PloyFuse; Digikey MF-MSMF050-2CT-ND
H1, H2, H3, H4: MountingHole_Pad; MountingHole_3mm_Pad_Via
J1: USB_B_Mini; USB_Mini_B_32005-201; Digikey ED2992CT-ND
J2: Conn_02x05_Odd_Even; 2x05_Prog_Header
L1, L2: FB; L_0402; Digikey 553-2374-1-ND‎
R1: 820; R_0805; Digikey 311-820ARCT-ND
R2: 10k; R_0603
R3, R4: 1k; R_0805; Digikey 311-1.0KARCT-ND
R5: 2.2k; R_0603
R6: 12k; R_0805; Digikey A129762CT-ND
R8, R9: 330; R_0805; Digikey A129743CT-ND
SW1, SW2: SW_DIP_x02; CTS_DPST_Switch; Digikey CT204211ST-ND
SW3: SW_DIP_x03; CTS_3DIP_Switch; Digikey CT2043ST-ND
U1: TLV1117-33; SOT-223-3_TabPin2; Digikey 296-50648-ND
U2: ISO7240; SOIC-16W_7.5x10.3mm_Pitch1.27mm; Digikey 296-22617-1-ND
U3: EEPROM_Array; SOT-23-6
U4: FT2232H; QFN-64-1EP_9x9mm_Pitch0.5mm; Digikey 768-1025-1-ND
U5: ISO7231; SOIC-16W_7.5x10.3mm_Pitch1.27mm; Digikey 296-22960-5-ND
U6: EEPROM_Array_8pin; EEPROM_8pin; Digikey 1662-2080-1-ND‎
Y1: 12MHz; Crystal_SMD_HC49-SD; Digikey XC2079CT-ND

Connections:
+1V8: C6.1, C7.1, C8.1, C9.1, U4.12, U4.37, U4.49, U4.64
+3V3: C4.1, C5.1, C10.2, C11.2, D2.2 (A), D3.2 (A), L1.1, L2.1, R1.1, R2.1, R3.1, SW1.1, U1.2 (VO), U2.1, U3.6, U4.20, U4.31, U4.42, U4.50, U4.56, U5.10, U5.16, U6.8
+5V: C3.1, F1.1, U1.3 (VI)
/3V3_MCU: J2.1, SW1.4, U2.10, U2.16, U5.1, U5.7
/D+: J1.3 (D+), U4.8
/D-: J1.2 (D-), U4.7
/FTDI_CLK: U3.4, U4.62, U6.2
/FTDI_CS: U3.5, U4.63, U6.1
/FTDI_DATA: R5.2, U3.3, U4.61, U6.3
/GPIO28: J2.3, SW2.4
/GPIO29: J2.5, SW2.3
/JTAG_TRST: SW3.4, U5.5
/SCI_RX: SW2.1, U2.11
/SCI_TX: SW2.2, U5.4
/TCK: J2.4, U2.14
/TDI: J2.8, U2.13
/TDO: J2.6, U5.3
/TMS: J2.2, U2.12
/TRST: J2.10, SW3.3
GND: J2.7, J2.9, SW1.3, U2.9, U2.15, U5.2, U5.8
GNDD: C1.2, C2.2, C3.2, C4.2, C5.2, C6.2, C7.2, C8.2, C9.2, C10.1, C11.1, C12.2, C13.2, D1.1 (K), J1.5 (GND), J1.6 (Shield), R4.2, R6.1, SW1.2, U1.1 (GND), U2.2, U2.8, U3.2, U4.1, U4.5, U4.10, U4.11, U4.13, U4.15, U4.25, U4.35, U4.47, U4.51, U4.65, U5.9, U5.15, U6.5, U6.6
unnamed: C1.1, L2.2, U4.4
unnamed: C2.1, L1.2, U4.9
unnamed: C12.1, U4.2, Y1.1
unnamed: C13.1, U4.3, Y1.2
unnamed: D1.2 (A), R1.2
unnamed: D2.1 (K), R8.1
unnamed: D3.1 (K), R9.1
unnamed: F1.2, J1.1 (VBUS)
unnamed: R2.2, R5.1, U3.1, U6.4
unnamed: R3.2, U4.14
unnamed: R4.1, U4.32
unnamed: R6.2, U4.6
unnamed: R8.2, U4.54
unnamed: R9.2, U4.55
unnamed: U2.3, U4.16
unnamed: U2.4, U4.17
unnamed: U2.5, U4.19
unnamed: U2.6, U4.38
unnamed: U4.18, U5.14
unnamed: U4.21, U5.12
unnamed: U4.39, U5.13
unnamed: U4.40, U4.41

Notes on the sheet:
Duplicate incase 8pin EEPROM does not work
PWR_ISO
XDS100 Serial
Boot Mode
Programming Cable Interface
Follows ARM 10 Pin JTAG Interface, slightly modified

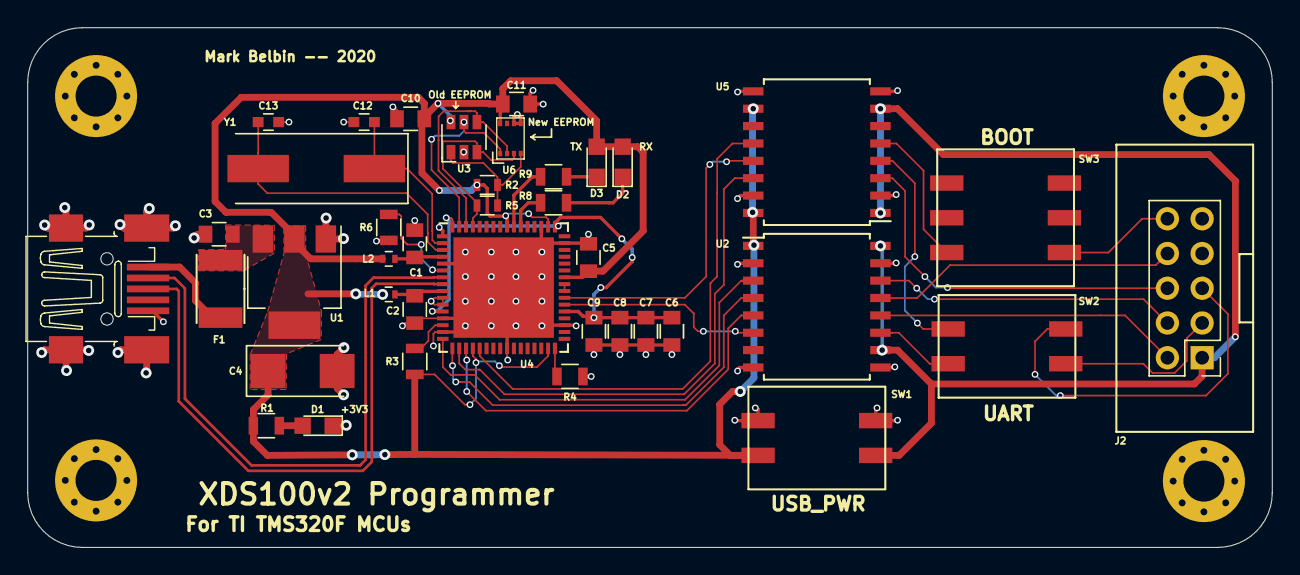
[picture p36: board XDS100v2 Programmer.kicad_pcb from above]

Board: 2 copper layers, 91.0 x 38.0 mm, 43 parts (0 on the bottom side), 43 nets.

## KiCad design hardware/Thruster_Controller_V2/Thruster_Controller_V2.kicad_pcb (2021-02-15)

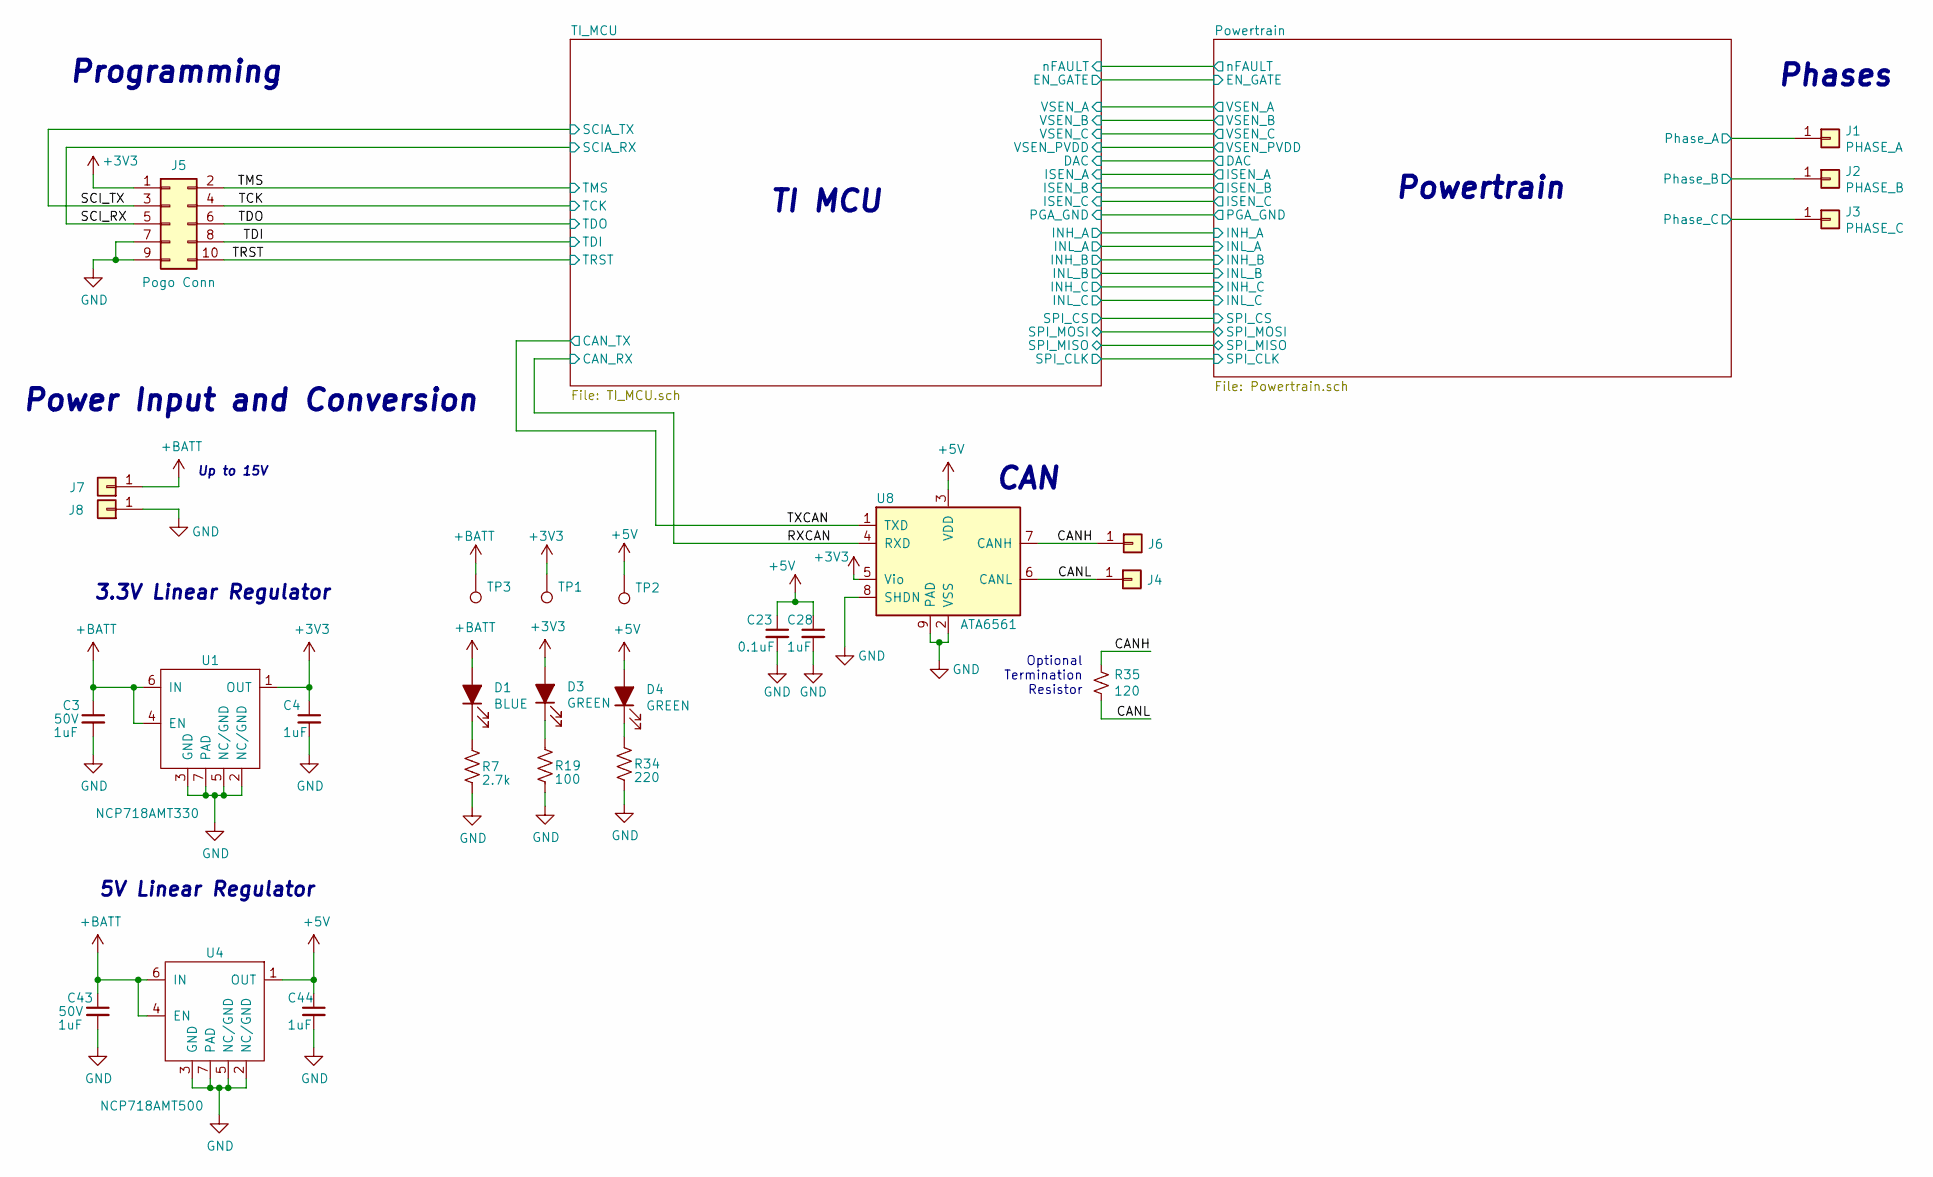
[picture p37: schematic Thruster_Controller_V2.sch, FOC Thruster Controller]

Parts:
C3, C43: 1uF; C_0805_2012Metric; Voltage 50V; Digikey 1276-6470-1-ND
C4, C28, C44: 1uF; C_0603_1608Metric; Digikey 1276-1102-1-ND
C23: 0.1uF; C_0402_1005Metric; Digikey 490-10698-1-ND
D1: BLUE; LED_0603_1608Metric; Digikey 732-4966-1-ND
D3, D4: GREEN; LED_0603_1608Metric; Digikey 732-4980-1-ND
J1: PHASE_A; Phase_Pad
J2: PHASE_B; Phase_Pad
J3: PHASE_C; Phase_Pad
J4, J6: Conn_01x01; CAN_Pad
J5: Pogo Conn; Tag-Connect_TC2050-IDC-NL
J7, J8: Conn_01x01; Bus_Pad
R7: 2.7k; R_0603_1608Metric; Digikey RMCF0603JT2K70CT-ND
R19: 100; R_0603_1608Metric; Digikey 2019-RK73B1JTTD101JCT-ND
R34: 220; R_0603_1608Metric; Digikey 2019-RK73B1JTTD221JCT-ND
R35: 120; R_0402_1005Metric; Digikey 311-120JRCT-ND
TP1, TP2, TP3: TestPoint; TestPoint_Pad_D1.0mm
U1: NCP718AMT330; DFN-6-1EP_2x2mm_P0.65mm_EP1x1.6mm; Digikey NCP718AMT330TBGOSCT-ND
U4: NCP718AMT500; DFN-6-1EP_2x2mm_P0.65mm_EP1x1.6mm; Digikey ‎NCP718AMT500TBGOSCT-ND‎
U8: ATA6561; DFN-8-1EP_3x3mm_P0.65mm_EP1.7x2.05mm; Digikey ATA6561-GBQW-NCT-ND

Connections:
+3V3: C4.1, D3.2 (A), J5.1, TP1.1, U1.1 (OUT), U8.5 (Vio); also elsewhere on the board
+5V: C23.1, C28.1, C44.1, D4.2 (A), TP2.1, U4.1 (OUT), U8.3 (VDD)
+BATT: C3.1, C43.1, D1.2 (A), J7.1, TP3.1, U1.4 (EN), U1.6 (IN), U4.4 (EN), U4.6 (IN); also elsewhere on the board
/CANH: J6.1, R35.2, U8.7 (CANH)
/CANL: J4.1, R35.1, U8.6 (CANL)
/Powertrain/Phase_A: J1.1; also elsewhere on the board
/Powertrain/Phase_B: J2.1; also elsewhere on the board
/Powertrain/Phase_C: J3.1; also elsewhere on the board
/RXCAN: U8.4 (RXD); also elsewhere on the board
/SCI_RX: J5.5; also elsewhere on the board
/SCI_TX: J5.3; also elsewhere on the board
/TCK: J5.4; also elsewhere on the board
/TDI: J5.8; also elsewhere on the board
/TDO: J5.6; also elsewhere on the board
/TMS: J5.2; also elsewhere on the board
/TRST: J5.10
/TXCAN: U8.1 (TXD); also elsewhere on the board
GND: C3.2, C4.2, C23.2, C28.2, C43.2, C44.2, J5.7, J5.9, J8.1, R7.2, R19.2, R34.2, U1.2 (NC/GND), U1.3 (GND), U1.5 (NC/GND), U1.7 (PAD), U4.2 (NC/GND), U4.3 (GND), U4.5 (NC/GND), U4.7 (PAD), U8.2 (VSS), U8.8 (SHDN), U8.9 (PAD); also elsewhere on the board
unnamed: D1.1 (K), R7.1
unnamed: D3.1 (K), R19.1
unnamed: D4.1 (K), R34.1

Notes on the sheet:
TI MCU
Powertrain
Power Input and Conversion
Programming
CAN
Phases
3.3V Linear Regulator
Up to 15V
Optional Termination Resistor
5V Linear Regulator

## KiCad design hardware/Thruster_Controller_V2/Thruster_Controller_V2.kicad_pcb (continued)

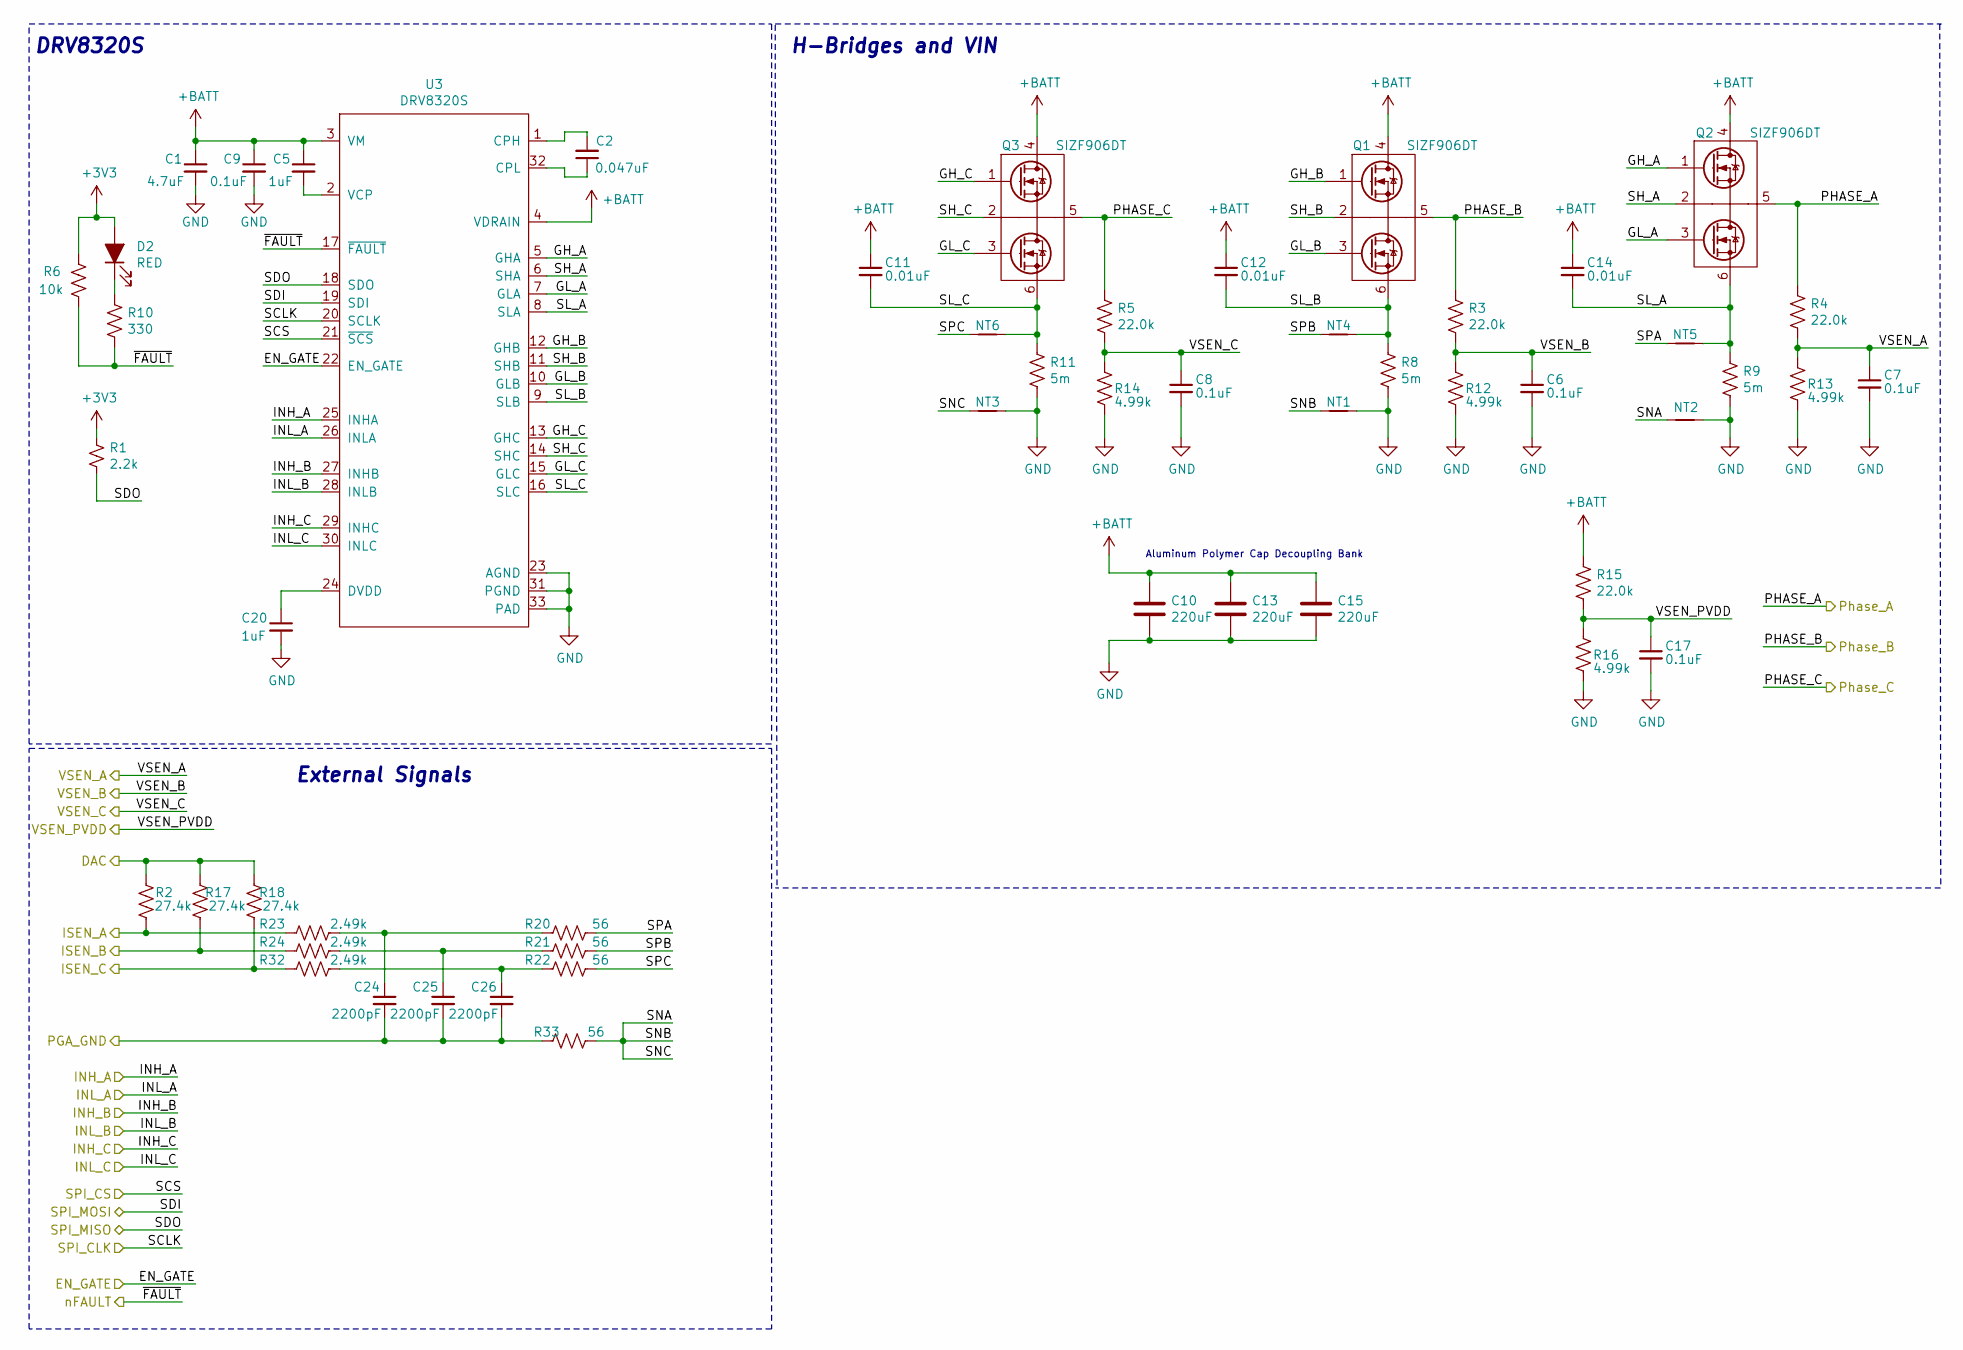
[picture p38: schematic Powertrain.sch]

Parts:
C1: 4.7uF; C_0603_1608Metric; Digikey 1276-1900-1-ND
C2: 0.047uF; C_0402_1005Metric; Digikey 490-10702-1-ND
C5, C20: 1uF; C_0603_1608Metric; Digikey 1276-1102-1-ND
C6, C7, C8, C9, C17: 0.1uF; C_0402_1005Metric; Digikey 490-10698-1-ND
C10, C13, C15: 220uF; CP_Elec_6.3x5.8; Digikey 565-APXJ160ARA221MF61GCT-ND
C11, C12, C14: 0.01uF; C_0402_1005Metric; Digikey 732-7545-1-ND
C24, C25, C26: 2200pF; C_0402_1005Metric; Digikey 490-6359-1-ND
D2: RED; LED_0603_1608Metric; Digikey 732-4978-1-ND
NT1, NT2, NT3, NT4, NT5, NT6: Net-Tie_2; NetTie-2_SMD_5mil
Q1, Q2, Q3: SIZF906DT; Digikey SIZF906DT-T1-GE3CT-ND
R1: 2.2k; R_0402_1005Metric; Digikey 311-2.2KJRCT-ND
R2, R17, R18: 27.4k; R_0402_1005Metric; Digikey RMCF0402FT27K4CT-ND
R3, R4, R5, R15: 22.0k; R_0402_1005Metric; Digikey RMCF0402FT22K0CT-ND
R6: 10k; R_0402_1005Metric; Digikey 2019-RK73B1ETTP103JCT-ND
R8, R9, R11: 5m; R_2512_6332Metric; Digikey YAG6105CT-ND
R10: 330; R_0603_1608Metric; Digikey RMCF0603JT330RCT-ND
R12, R13, R14, R16: 4.99k; R_0402_1005Metric; Digikey 311-4.99KLRCT-ND
R20, R21, R22, R33: 56; R_0402_1005Metric; Digikey 311-56JRCT-ND
R23, R24, R32: 2.49k; R_0402_1005Metric; Digikey RMCF0402FT2K49CT-ND
U3: DRV8320S; WQFN-32-1EP_5x5mm_P0.5mm_EP3.1x3.1mm; Digikey 296-50725-1-ND

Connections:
+3V3: D2.2 (A), R1.1, R6.1; also elsewhere on the board
+BATT: C1.1, C5.1, C9.1, C10.1, C11.1, C12.1, C13.1, C14.1, C15.1, Q1.4 (Vin/D1), Q2.4 (Vin/D1), Q3.4 (Vin/D1), R15.1, U3.3 (VM), U3.4 (VDRAIN); also elsewhere on the board
/Powertrain/DAC: R2.2, R17.2, R18.2; also elsewhere on the board
/Powertrain/EN_GATE: U3.22 (EN_GATE); also elsewhere on the board
/Powertrain/GH_A: Q2.1 (GHS/G1), U3.5 (GHA)
/Powertrain/GH_B: Q1.1 (GHS/G1), U3.12 (GHB)
/Powertrain/GH_C: Q3.1 (GHS/G1), U3.13 (GHC)
/Powertrain/GL_A: Q2.3 (GLS/G2), U3.7 (GLA)
/Powertrain/GL_B: Q1.3 (GLS/G2), U3.10 (GLB)
/Powertrain/GL_C: Q3.3 (GLS/G2), U3.15 (GLC)
/Powertrain/INH_A: U3.25 (INHA); also elsewhere on the board
/Powertrain/INH_B: U3.27 (INHB); also elsewhere on the board
/Powertrain/INH_C: U3.29 (INHC); also elsewhere on the board
/Powertrain/INL_A: U3.26 (INLA); also elsewhere on the board
/Powertrain/INL_B: U3.28 (INLB); also elsewhere on the board
/Powertrain/INL_C: U3.30 (INLC); also elsewhere on the board
/Powertrain/ISEN_A: R2.1, R23.2; also elsewhere on the board
/Powertrain/ISEN_B: R17.1, R24.2; also elsewhere on the board
/Powertrain/ISEN_C: R18.1, R32.2; also elsewhere on the board
/Powertrain/PGA_GND: C24.2, C25.2, C26.2, R33.2; also elsewhere on the board
/Powertrain/Phase_A: Q2.5 (VSW/S1-D2), R4.1; also elsewhere on the board
/Powertrain/Phase_B: Q1.5 (VSW/S1-D2), R3.1; also elsewhere on the board
/Powertrain/Phase_C: Q3.5 (VSW/S1-D2), R5.1; also elsewhere on the board
/Powertrain/SH_A: Q2.2 (Return/S1), U3.6 (SHA)
/Powertrain/SH_B: Q1.2 (Return/S1), U3.11 (SHB)
/Powertrain/SH_C: Q3.2 (Return/S1), U3.14 (SHC)
/Powertrain/SL_A: C14.2, NT5.2, Q2.6 (GND/S2), R9.1, U3.8 (SLA)
/Powertrain/SL_B: C12.2, NT4.2, Q1.6 (GND/S2), R8.1, U3.9 (SLB)
/Powertrain/SL_C: C11.2, NT6.2, Q3.6 (GND/S2), R11.1, U3.16 (SLC)
/Powertrain/SNA: NT1.1, NT2.1, NT3.1, R33.1
/Powertrain/SPA: NT5.1, R20.1
/Powertrain/SPB: NT4.1, R21.1
/Powertrain/SPC: NT6.1, R22.1
/Powertrain/SPI_CLK: U3.20 (SCLK); also elsewhere on the board
/Powertrain/SPI_CS: U3.21 (~SCS~); also elsewhere on the board
/Powertrain/SPI_MISO: R1.2, U3.18 (SDO); also elsewhere on the board
/Powertrain/SPI_MOSI: U3.19 (SDI); also elsewhere on the board
/Powertrain/VSEN_A: C7.1, R4.2, R13.1; also elsewhere on the board
/Powertrain/VSEN_B: C6.1, R3.2, R12.1; also elsewhere on the board
/Powertrain/VSEN_C: C8.1, R5.2, R14.1; also elsewhere on the board
/Powertrain/VSEN_PVDD: C17.1, R15.2, R16.1; also elsewhere on the board
/Powertrain/nFAULT: R6.2, R10.2, U3.17 (~FAULT~); also elsewhere on the board
GND: C1.2, C6.2, C7.2, C8.2, C9.2, C10.2, C13.2, C15.2, C17.2, C20.2, NT1.2, NT2.2, NT3.2, R8.2, R9.2, R11.2, R12.2, R13.2, R14.2, R16.2, U3.23 (AGND), U3.31 (PGND), U3.33 (PAD); also elsewhere on the board
unnamed: C2.1, U3.32 (CPL)
unnamed: C2.2, U3.1 (CPH)
unnamed: C5.2, U3.2 (VCP)
unnamed: C20.1, U3.24 (DVDD)
unnamed: C24.1, R20.2, R23.1
unnamed: C25.1, R21.2, R24.1
unnamed: C26.1, R22.2, R32.1
unnamed: D2.1 (K), R10.1

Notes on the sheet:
H-Bridges and VIN
External Signals
DRV8320S
Aluminum Polymer Cap Decoupling Bank

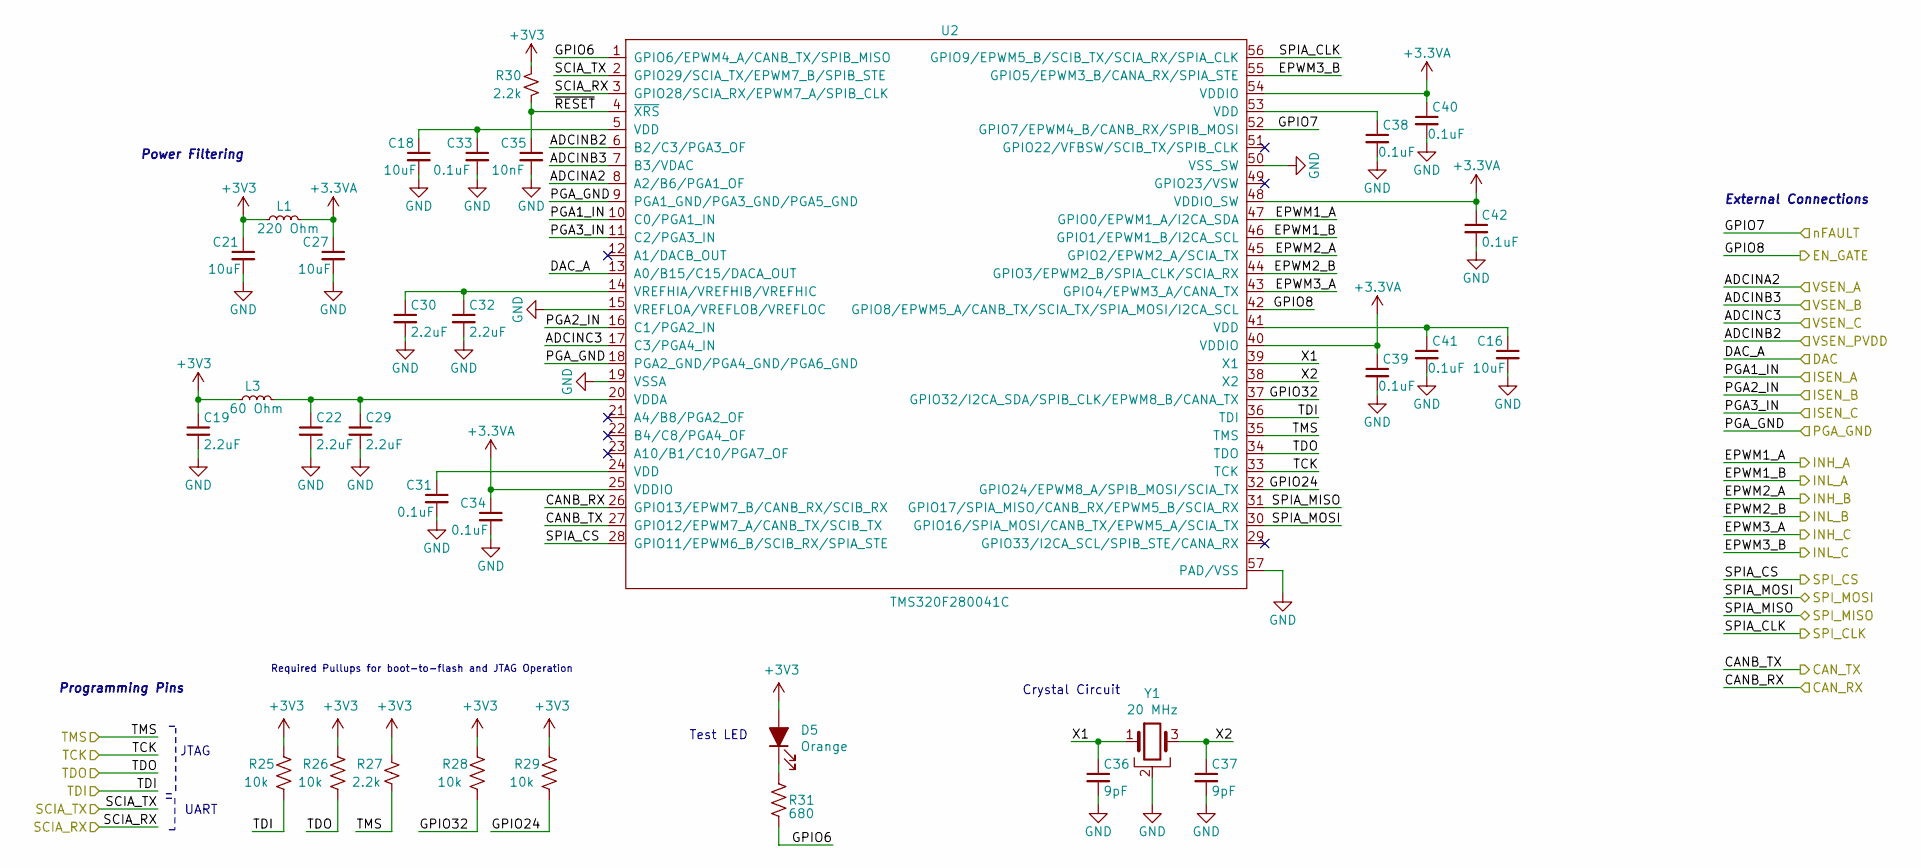
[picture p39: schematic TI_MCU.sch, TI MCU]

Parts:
C16, C18, C21, C27: 10uF; C_0603_1608Metric; Digikey 1276-1119-1-ND
C19, C22, C29, C30, C32: 2.2uF; C_0402_1005Metric; Digikey 490-10451-1-ND
C31, C33, C34, C38, C39, C40, C41, C42: 0.1uF; C_0402_1005Metric; Digikey 490-10698-1-ND
C35: 10nF; C_0402_1005Metric; Digikey 732-7545-1-ND
C36, C37: 9pF; C_0402_1005Metric; Digikey 490-5880-1-ND
D5: Orange; LED_0603_1608Metric; Digikey 160-1180-1-ND
L1: 220 Ohm; L_0402_1005Metric; Digikey 490-11021-1-ND
L3: 60 Ohm; L_0402_1005Metric; Digikey 445-172882-1-ND
R25, R26, R28, R29: 10k; R_0402_1005Metric; Digikey 2019-RK73B1ETTP103JCT-ND
R27, R30: 2.2k; R_0402_1005Metric; Digikey 311-2.2KJRCT-ND
R31: 680; R_0603_1608Metric; Digikey RMCF0603JT680RCT-ND
U2: TMS320F280041C; QFN-56-1EP_7x7mm_P0.4mm_EP5.6x5.6mm; Digikey 296-F280041CRSHSRCT-ND
Y1: 20 MHz; Crystal_SMD_SeikoEpson_FA238-4pin_3.2x2.5mm; Digikey SER3629CT-ND

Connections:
+3.3VA: C27.1, C34.1, C39.1, C40.1, C42.1, L1.2, U2.25 (VDDIO), U2.40 (VDDIO), U2.48 (VDDIO_SW), U2.54 (VDDIO)
+3V3: C19.1, C21.1, D5.2 (A), L1.1, L3.1, R25.1, R26.1, R27.1, R28.1, R29.1, R30.1; also elsewhere on the board
/Powertrain/DAC: U2.13 (A0/B15/C15/DACA_OUT); also elsewhere on the board
/Powertrain/EN_GATE: U2.42 (GPIO8/EPWM5_A/CANB_TX/SCIA_TX/SPIA_MOSI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); also elsewhere on the board
/Powertrain/INH_A: U2.47 (GPIO0/EPWM1_A/I2CA_SDA); also elsewhere on the board
/Powertrain/INH_B: U2.45 (GPIO2/EPWM2_A/SCIA_TX); also elsewhere on the board
/Powertrain/INH_C: U2.43 (GPIO4/EPWM3_A/CANA_TX); also elsewhere on the board
/Powertrain/INL_A: U2.46 (GPIO1/EPWM1_B/I2CA_SCL); also elsewhere on the board
/Powertrain/INL_B: U2.44 (GPIO3/EPWM2_B/SPIA_CLK/SCIA_RX); also elsewhere on the board
/Powertrain/INL_C: U2.55 (GPIO5/EPWM3_B/CANA_RX/SPIA_STE); also elsewhere on the board
/Powertrain/ISEN_A: U2.10 (C0/PGA1_IN); also elsewhere on the board
/Powertrain/ISEN_B: U2.16 (C1/PGA2_IN); also elsewhere on the board
/Powertrain/ISEN_C: U2.11 (C2/PGA3_IN); also elsewhere on the board
/Powertrain/PGA_GND: U2.9 (PGA1_GND/PGA3_GND/PGA5_GND), U2.18 (PGA2_GND/PGA4_GND/PGA6_GND); also elsewhere on the board
/Powertrain/SPI_CLK: U2.56 (GPIO9/EPWM5_B/SCIB_TX/SCIA_RX/SPIA_CLK); also elsewhere on the board
/Powertrain/SPI_CS: U2.28 (GPIO11/EPWM6_B/SCIB_RX/SPIA_STE); also elsewhere on the board
/Powertrain/SPI_MISO: U2.31 (GPIO17/SPIA_MISO/CANB_RX/EPWM5_B/SCIA_RX); also elsewhere on the board
/Powertrain/SPI_MOSI: U2.30 (GPIO16/SPIA_MOSI/CANB_TX/EPWM5_A/SCIA_TX); also elsewhere on the board
/Powertrain/VSEN_A: U2.8 (A2/B6/PGA1_OF); also elsewhere on the board
/Powertrain/VSEN_B: U2.7 (B3/VDAC); also elsewhere on the board
/Powertrain/VSEN_C: U2.17 (C3/PGA4_IN); also elsewhere on the board
/Powertrain/VSEN_PVDD: U2.6 (B2/C3/PGA3_OF); also elsewhere on the board
/Powertrain/nFAULT: U2.52 (GPIO7/EPWM4_B/CANB_RX/SPIB_MOSI); also elsewhere on the board
/RXCAN: U2.26 (GPIO13/EPWM7_B/CANB_RX/SCIB_RX); also elsewhere on the board
/SCI_RX: U2.3 (GPIO28/SCIA_RX/EPWM7_A/SPIB_CLK); also elsewhere on the board
/SCI_TX: U2.2 (GPIO29/SCIA_TX/EPWM7_B/SPIB_STE); also elsewhere on the board
/TCK: U2.33 (TCK); also elsewhere on the board
/TDI: R25.2, U2.36 (TDI); also elsewhere on the board
/TDO: R26.2, U2.34 (TDO); also elsewhere on the board
/TI_MCU/GPIO6: R31.2, U2.1 (GPIO6/EPWM4_A/CANB_TX/SPIB_MISO)
/TI_MCU/GPIO24: R29.2, U2.32 (GPIO24/EPWM8_A/SPIB_MOSI/SCIA_TX)
/TI_MCU/GPIO32: R28.2, U2.37 (GPIO32/I2CA_SDA/SPIB_CLK/EPWM8_B/CANA_TX)
/TI_MCU/X1: C36.1, U2.39 (X1), Y1.1
/TI_MCU/X2: C37.1, U2.38 (X2), Y1.3
/TI_MCU/~RESET~: C35.1, R30.2, U2.4 (~XRS~)
/TMS: R27.2, U2.35 (TMS); also elsewhere on the board
/TXCAN: U2.27 (GPIO12/EPWM7_A/CANB_TX/SCIB_TX); also elsewhere on the board
GND: C16.2, C18.2, C19.2, C21.2, C22.2, C27.2, C29.2, C30.2, C31.2, C32.2, C33.2, C34.2, C35.2, C36.2, C37.2, C38.2, C39.2, C40.2, C41.2, C42.2, U2.15 (VREFLOA/VREFLOB/VREFLOC), U2.19 (VSSA), U2.50 (VSS_SW), U2.57 (PAD/VSS), Y1.2; also elsewhere on the board
unnamed: C16.1, C41.1, U2.41 (VDD)
unnamed: C18.1, C33.1, U2.5 (VDD)
unnamed: C22.1, C29.1, L3.2, U2.20 (VDDA)
unnamed: C30.1, C32.1, U2.14 (VREFHIA/VREFHIB/VREFHIC)
unnamed: C31.1, U2.24 (VDD)
unnamed: C38.1, U2.53 (VDD)
unnamed: D5.1 (K), R31.1

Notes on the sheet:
Required Pullups for boot-to-flash and JTAG Operation
External Connections
Programming Pins
JTAG
UART
Test LED
Crystal Circuit
Power Filtering

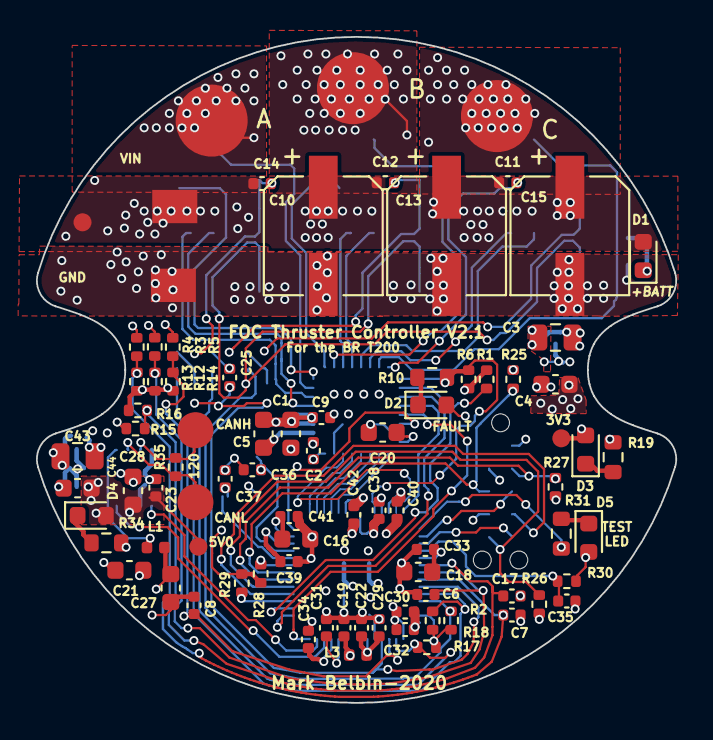
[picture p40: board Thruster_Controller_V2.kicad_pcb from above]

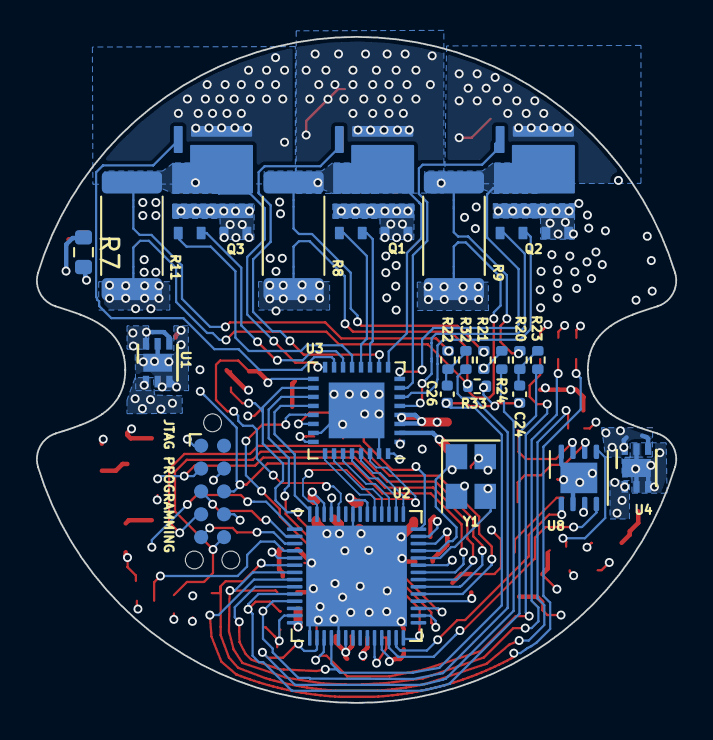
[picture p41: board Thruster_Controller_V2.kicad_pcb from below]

Board: 4 copper layers, 35.5 x 37.0 mm, 112 parts (29 on the bottom side), 79 nets.

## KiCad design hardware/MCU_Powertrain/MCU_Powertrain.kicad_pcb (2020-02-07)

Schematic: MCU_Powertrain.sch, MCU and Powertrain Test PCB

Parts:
C21, C22: 15pF; C_0603; Digikey 311-1060-1-ND
C23, C30, C33, C42: 0.1uF; C_0603; Digikey 1276-CL10B104KB8NNNLCT-ND
C28, C29, C40, C41: 1uF; C_0805; Digikey 399-8011-1-ND
C31: 22uF; C_0805; Digikey 490-14661-1-ND
C32: 0.33uF; C_0603; Digikey 1276-2370-1-ND
C39: 1.01uF; C_0805; Voltage 35V; Digikey 311-1909-1-ND
D3: GREEN; LED_0603; Digikey 160-1446-1-ND
D4: D_Schottky_ALT; D_SOD-123F; Digikey MBR1H100SFT3GOSCT-ND
H1, H2, H3, H4: MountingHole; MountingHole_3mm_Pad_Via
J1: PHASE_A; 3mm_Bullet_RA
J2: PHASE_B; 3mm_Bullet_RA
J3: PHASE_C; 3mm_Bullet_RA
J4: Big Conn; 2x05_Prog_Header; Digikey 302-S101
J5: Pogo Conn; Tag-Connect_TC2050-IDC-NL
J6: Conn CAN; 70553-03; Digikey WM4901-ND
J7: PWRIN; AMASS_XT60-M
L1: 15uH; Eaton_Inductor; Digikey 513-1458-1-ND
R17, R18: 10k; R_0805; Digikey 311-10.0KCRCT-ND
R19: 330; R_0603; Digikey RHM330DCT-ND
R23: 68.0k; R_0603; Digikey P68KDBCT-ND
R24: 20.0k; R_0603; Digikey P20KDBCT-ND
R35: 120; R_0805; Digikey A129738CT-ND
TP1, TP2, TP3: TestPoint; TestPoint_Loop_D1.80mm_Drill1.0mm_Beaded; Digikey 36-5117-ND
TP4, TP16, TP17, TP19, TP21: TestPoint; TestPoint_Loop_D1.80mm_Drill1.0mm_Beaded; Digikey 36-5001-ND
TP5, TP6, TP7, TP8, TP9, TP10, TP11, TP12, TP13, TP14, TP15: TestPoint; TestPoint_Loop_D1.80mm_Drill1.0mm_Beaded; Digikey 36-5119-ND
TP18, TP20: TestPoint; TestPoint_Loop_D1.80mm_Drill1.0mm_Beaded; Digikey 36-5000-ND
U2: RTQ2569-50GQW; DFN-8-1EP_3x3mm_Pitch0.65mm; Digikey 1028-1523-1-ND
U3: MCP2515; QFN-20-1EP_4x4mm_Pitch0.5mm; Digikey MCP2515T-I/MLCT-ND
U4: LMR16006XDDC; SOT-23-6; Digikey 296-40293-1-ND
U8: MCP2562; DFN-8-1EP_3x3mm_Pitch0.65mm; Digikey MCP2562-E/MF-ND
Y1: 20MHz; Crystal_SMD_SeikoEpson_TSX3225-4pin_3.2x2.5mm; Digikey SER4249CT-ND

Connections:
+3V3: C23.1, C28.1, C31.2, C42.1, D3.2 (A), J4.1, J5.1, L1.2, R17.1, R18.1, R23.1, TP18.1, U3.18 (VDD), U8.5 (Vio); also elsewhere on the board
+5V: C29.1, C30.1, C40.1, C41.1, U2.6 (Vout), U8.3 (VDD)
+BATT: C33.1, C39.1, J7.2, TP20.1, U2.1 (VIN), U2.8 (EN), U4.5; also elsewhere on the board
/CANH: J6.1, R35.2, TP6.1, U8.7 (CANH)
/CANL: J6.2, R35.1, TP10.1, U8.6 (CANL)
/GPIO28: J4.3, J5.3, TP12.1; also elsewhere on the board
/GPIO29: J4.5, J5.5, TP14.1; also elsewhere on the board
/Powertrain/Phase_A: J1.1, TP3.1; also elsewhere on the board
/Powertrain/Phase_B: J2.1, TP2.1; also elsewhere on the board
/Powertrain/Phase_C: J3.1, TP1.1; also elsewhere on the board
/Powertrain/SPI_CLK: U3.12 (SCK); also elsewhere on the board
/Powertrain/SPI_MISO: U3.15 (SO); also elsewhere on the board
/Powertrain/SPI_MOSI: U3.14 (SI); also elsewhere on the board
/RXCAN: TP8.1, U3.20 (RXCAN), U8.4 (RXD)
/TCK: J4.4, J5.4, TP13.1; also elsewhere on the board
/TDI: J4.8, J5.8, TP9.1; also elsewhere on the board
/TDO: J4.6, J5.6, TP11.1; also elsewhere on the board
/TI_MCU/CAN_INT: R17.2, U3.11 (~INT); also elsewhere on the board
/TI_MCU/SPI_CS_1: U3.16 (~CS); also elsewhere on the board
/TMS: J4.2, J5.2, TP15.1; also elsewhere on the board
/TRST: J4.10, J5.10, TP7.1; also elsewhere on the board
/TXCAN: TP5.1, U3.19 (TXCAN), U8.1 (TXD)
GND: C21.2, C22.2, C23.2, C28.2, C29.2, C30.2, C31.1, C33.2, C39.2, C40.2, C41.2, C42.2, D4.2 (A), J4.7, J4.9, J5.7, J5.9, J6.3, J7.1, R19.2, R24.2, TP4.1, TP16.1, TP17.1, TP19.1, TP21.1, U2.3 (GND), U2.9 (EP), U3.8 (VSS), U3.21 (PAD), U4.2, U8.2 (VSS), U8.8 (SHDN), U8.9 (PAD), Y1.2, Y1.4; also elsewhere on the board
unnamed: C21.1, U3.6 (OSC2), Y1.3
unnamed: C22.1, U3.7 (OSC1), Y1.1
unnamed: C32.1, D4.1 (K), L1.1, U4.6
unnamed: C32.2, U4.1
unnamed: D3.1 (K), R19.1
unnamed: R18.2, U3.17 (~RESET)
unnamed: R23.2, R24.1, U4.3

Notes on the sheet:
TI MCU
Powertrain
Power Input
Programming
CAN
Phases
3.3V Regulator
Up to 24V
Termination Resistor
CAN chips decoupling cap
5V LDO


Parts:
C34, C35, C36, C37, C38: 2.2uF; C_0805; Digikey 1276-1763-1-ND
D5, D6, D7, D8: BLUE; LED_0805; Digikey 732-4982-1-ND
L2: FB; L_0805; Digikey 240-2549-1-ND
L3: FB; L_0402; Digikey 445-172882-1-ND
R25, R26: 820; R_0805; Digikey 311-820ARCT-ND
R27, R28, R29, R30: 2.2k; R_0805; Digikey 541-4139-1-ND
R31, R32, R33, R34: 330; R_0805; Digikey A129743CT-ND
SW1, SW2: SW_Push; SW_SPST_EVQQ2; Digikey CKN9112CT-ND
TP22, TP23, TP24, TP25, TP26, TP27, TP28: TestPoint; TestPoint_Loop_D1.80mm_Drill1.0mm_Beaded; Digikey 36-5117-ND
TP29, TP30, TP31, TP32, TP33, TP34: TestPoint; TestPoint_Loop_D1.80mm_Drill1.0mm_Beaded; Digikey 36-5116-ND
TP35, TP36, TP37, TP38, TP39, TP40: TestPoint; TestPoint_Loop_D1.80mm_Drill1.0mm_Beaded; Digikey 36-5119-ND
TP41, TP42, TP43, TP44: TestPoint; TestPoint_Loop_D1.80mm_Drill1.0mm_Beaded; Digikey 36-5001-ND
U5: TMS320F28027F; LQFP-48_7x7mm_Pitch0.5mm; Digikey 296-36409-ND
U6, U7: SN74LVC2G07; VSSOP-8_2.4x2.1mm_Pitch0.5mm; Digikey 296-13494-1-ND

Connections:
+3V3: C35.1, L2.1, L3.1, R25.1, R26.1, R30.1, R31.1, R32.1, R33.1, R34.1, U6.5 (VCC), U7.5 (VCC); also elsewhere on the board
/GPIO28: U5.48 (GPIO28/SCIRXDA/SDAA/~TZ2~); also elsewhere on the board
/GPIO29: U5.1 (GPIO29/SCITXDA/SCLA/~TZ3~); also elsewhere on the board
/Powertrain/EN_GATE: U5.41 (GPIO6/EPWM4A/EPWMSYNCI/EPWMSYNCO); also elsewhere on the board
/Powertrain/PWRGD: R30.2, SW1.2, U5.3 (~XRS~); also elsewhere on the board
/Powertrain/SPI_CLK: TP39.1, U5.24 (GPIO18/SPICLKA/SCITXDA/XCLKOUT); also elsewhere on the board
/Powertrain/SPI_CS_0: TP35.1, U5.25 (GPIO19/XCLKIN/~SPISTEA~/SCIRXDA/ECAP1); also elsewhere on the board
/Powertrain/SPI_MISO: TP38.1, U5.26 (GPIO17/SPISOMIA/~TZ3); also elsewhere on the board
/Powertrain/SPI_MOSI: TP37.1, U5.27 (GPIO16/SPISIMOA/~TZ2~); also elsewhere on the board
/TCK: U5.23 (TCK/XCLKIN/GPIO38); also elsewhere on the board
/TDI: U5.20 (TDI/GPIO35); also elsewhere on the board
/TDO: R25.2, R28.1, U5.22 (TDO/GPIO37); also elsewhere on the board
/TI_MCU/ADCINA0: TP25.1, U5.10 (ADCINA0/VREFHI); also elsewhere on the board
/TI_MCU/ADCINA1: TP24.1, U5.8 (ADCINA1); also elsewhere on the board
/TI_MCU/ADCINA2: U5.9 (ADCINA2/COMP1A/AIO2)
/TI_MCU/ADCINA3: TP23.1, U5.7 (ADCINA3); also elsewhere on the board
/TI_MCU/ADCINA4: U5.5 (ADCINA4/COMP2A/AIO4)
/TI_MCU/ADCINA6: U5.4 (ADCINA6/AIO6)
/TI_MCU/ADCINA7: TP22.1, U5.6 (ADCINA7); also elsewhere on the board
/TI_MCU/ADCINB1: TP26.1, U5.13 (ADCINB1); also elsewhere on the board
/TI_MCU/ADCINB2: U5.14 (ADCINB2/COMP1B/AIO10)
/TI_MCU/ADCINB3: TP27.1, U5.15 (ADCINB3); also elsewhere on the board
/TI_MCU/ADCINB4: U5.16 (ADCINB4/COMP2B/AIO12)
/TI_MCU/ADCINB6: U5.17 (ADCINB6/AIO14)
/TI_MCU/ADCINB7: TP28.1, U5.18 (ADCINB7); also elsewhere on the board
/TI_MCU/CAN_INT: SW2.1, TP40.1, U5.47 (GPIO12/~TZ1~/SCITXDA); also elsewhere on the board
/TI_MCU/EPWM1A: TP29.1, U5.29 (GPIO0/EPWM1A), U6.1 (1A); also elsewhere on the board
/TI_MCU/EPWM1B: TP30.1, U5.28 (GPIO1/EPWM1B/COMP1OUT), U6.3 (2A); also elsewhere on the board
/TI_MCU/EPWM2A: TP31.1, U5.37 (GPIO2/EPWM2A), U7.1 (1A); also elsewhere on the board
/TI_MCU/EPWM2B: TP32.1, U5.38 (GPIO3/EPWM2B/COMP2OUT), U7.3 (2A); also elsewhere on the board
/TI_MCU/EPWM3A: TP33.1, U5.39 (GPIO4/EPWM3A); also elsewhere on the board
/TI_MCU/EPWM3B: TP34.1, U5.40 (GPIO5/EPWM3B/ECAP1); also elsewhere on the board
/TI_MCU/GPIO7: U5.42 (GPIO7/EPWM4B/SCIRXDA); also elsewhere on the board
/TI_MCU/GPIO33: U5.36 (GPIO33/SCLA/EPWMSYNCO/~ADCSOCBO~)
/TI_MCU/GPIO34: R26.2, R29.1, U5.19 (GPIO34/COMP2OUT)
/TI_MCU/SPI_CS_1: TP36.1, U5.31 (GPIO32/SDAA/EPWMSYNCI/~ADCSOCAO~); also elsewhere on the board
/TMS: U5.21 (TMS/GPIO36); also elsewhere on the board
/TRST: R27.1, U5.2 (~TRST~); also elsewhere on the board
GND: C34.2, C35.2, C36.2, C37.2, C38.2, R27.2, R28.2, R29.2, SW1.1, SW2.2, TP41.1, TP42.1, TP43.1, TP44.1, U5.12 (VSSA/VREFLO), U5.30 (TEST), U5.33 (VSS1), U5.34 (~VREGENZ~), U5.44 (VSS2), U6.2 (GND), U7.2 (GND); also elsewhere on the board
unnamed: C34.1, U5.43 (VDD2)
unnamed: C36.1, L2.2, U5.11 (VDDA)
unnamed: C37.1, L3.2, U5.35 (VDDIO)
unnamed: C38.1, U5.32 (VDD1)
unnamed: D5.1 (K), U6.6 (1Y)
unnamed: D5.2 (A), R31.2
unnamed: D6.1 (K), U6.4 (2Y)
unnamed: D6.2 (A), R32.2
unnamed: D7.1 (K), U7.6 (1Y)
unnamed: D7.2 (A), R33.2
unnamed: D8.1 (K), U7.4 (2Y)
unnamed: D8.2 (A), R34.2

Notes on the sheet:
No External Cystral Required
Same LED outputs as original LaunchPad Dev board
Required Pullups/Pulldowns for XDS100v2 operation and boot-to-flash (XDS100v2 disconnected)
External Connections
Programming Pins
JTAG
UART
For Dev Only

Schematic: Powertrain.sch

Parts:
C1: 4.7uF; C_0603; Digikey 1276-1900-1-ND
C2, C4: 0.047uF; C_0402; Digikey 490-10702-1-ND
C3, C5, C20, C27: 1uF; C_0603; Digikey 1276-1102-1-ND
C6, C7, C8, C17: 0.1uF; C_0603; Digikey 1276-CL10B104KB8NNNLCT-ND
C9, C16, C18: 1000pF; C_0402; Digikey 311-1036-1-ND
C10, C11, C12: 220uF; CP_Elec_8x10.5; Digikey 25PEV220M8X10.5CT-ND
C13, C14, C15: 22uF; C_0805; Digikey 490-14661-1-ND
C19: 2.2uF; C_0603; Digikey 490-10731-1-ND
C24, C25, C26: 2200pF; C_0603; Digikey 490-1459-1-ND
D1: BLUE; LED_0603; Digikey 160-1827-1-ND
D2: RED; LED_0603; Digikey 160-1447-1-ND
NT1, NT2, NT3, NT4, NT5, NT6: Net-Tie_2; NetTie-2_SMD_5mil
Q1, Q2, Q3: SIZF906DT; Digikey SIZF906DT-T1-GE3CT-ND
R1, R6: 10k; R_0603; Digikey RNCP0603FTD10K0CT-ND
R2: 100; R_0603; Digikey RHM100DCT-ND
R3, R4, R5, R15: 22.0k; R_0603; Digikey P22KDBCT-ND
R7: 2.7k; R_0603; Digikey P2.7KDACT-ND
R8, R9, R11: 5m; R_2512_Sense; Digikey YAG6124CT-ND
R10: 330; R_0603; Digikey RHM330DCT-ND
R12, R13, R14, R16: 4.99k; R_0603; Digikey P4.99KDBCT-ND
R20, R21, R22: 56; R_0603; Digikey A129673CT-ND
U1: DRV8305; Digikey 296-42659-1-ND

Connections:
+3V3: C27.1, D2.2 (A), R1.1, R6.1, U1.48; also elsewhere on the board
+BATT: C1.1, C10.1, C11.1, C12.1, C13.2, C14.2, C15.2, C19.1, D1.2 (A), Q1.4, Q2.4, Q3.4, R2.1, R15.1, U1.41; also elsewhere on the board
/GPIO28: R6.2, R10.2, U1.8; also elsewhere on the board
/Powertrain/EN_GATE: U1.1; also elsewhere on the board
/Powertrain/GH_A: Q3.1, U1.36
/Powertrain/GH_B: Q1.1, U1.29
/Powertrain/GH_C: Q2.1, U1.28
/Powertrain/GL_A: Q3.3, U1.33
/Powertrain/GL_B: Q1.3, U1.32
/Powertrain/GL_C: Q2.3, U1.25
/Powertrain/ISEN_A_DRV: R20.1, U1.16
/Powertrain/ISEN_B_DRV: R21.1, U1.17
/Powertrain/ISEN_C_DRV: R22.1, U1.18
/Powertrain/PWRGD: R1.2, U1.13; also elsewhere on the board
/Powertrain/Phase_A: Q3.5, R5.1; also elsewhere on the board
/Powertrain/Phase_B: Q1.5, R3.1; also elsewhere on the board
/Powertrain/Phase_C: Q2.5, R4.1; also elsewhere on the board
/Powertrain/SH_A: Q3.2, U1.35
/Powertrain/SH_B: Q1.2, U1.30
/Powertrain/SH_C: Q2.2, U1.27
/Powertrain/SL_A: NT6.2, Q3.6, R11.1, U1.34
/Powertrain/SL_B: NT4.2, Q1.6, R8.1, U1.31
/Powertrain/SL_C: NT5.2, Q2.6, R9.1, U1.26
/Powertrain/SN1: C9.1, NT6.1, U1.23
/Powertrain/SN2: C16.1, NT4.1, U1.21
/Powertrain/SN3: C18.1, NT5.1, U1.19
/Powertrain/SP1: C9.2, NT3.1, U1.24
/Powertrain/SP2: C16.2, NT1.1, U1.22
/Powertrain/SP3: C18.2, NT2.1, U1.20
/Powertrain/SPI_CLK: U1.12; also elsewhere on the board
/Powertrain/SPI_CS_0: U1.9; also elsewhere on the board
/Powertrain/SPI_MISO: U1.11; also elsewhere on the board
/Powertrain/SPI_MOSI: U1.10; also elsewhere on the board
/TI_MCU/ADCINA0: C17.1, R15.2, R16.1; also elsewhere on the board
/TI_MCU/ADCINA1: C7.1, R4.2, R13.1; also elsewhere on the board
/TI_MCU/ADCINA3: C6.1, R3.2, R12.1; also elsewhere on the board
/TI_MCU/ADCINA7: C8.1, R5.2, R14.1; also elsewhere on the board
/TI_MCU/ADCINB1: C24.1, R20.2; also elsewhere on the board
/TI_MCU/ADCINB3: C25.1, R21.2; also elsewhere on the board
/TI_MCU/ADCINB7: C26.1, R22.2; also elsewhere on the board
/TI_MCU/EPWM1A: U1.2; also elsewhere on the board
/TI_MCU/EPWM1B: U1.3; also elsewhere on the board
/TI_MCU/EPWM2A: U1.4; also elsewhere on the board
/TI_MCU/EPWM2B: U1.5; also elsewhere on the board
/TI_MCU/EPWM3A: U1.6; also elsewhere on the board
/TI_MCU/EPWM3B: U1.7; also elsewhere on the board
/TI_MCU/GPIO7: U1.47; also elsewhere on the board
GND: C1.2, C3.2, C5.2, C6.2, C7.2, C8.2, C10.2, C11.2, C12.2, C13.1, C14.1, C15.1, C17.2, C20.2, C24.2, C25.2, C26.2, C27.2, NT1.2, NT2.2, NT3.2, R7.2, R8.2, R9.2, R11.2, R12.2, R13.2, R14.2, R16.2, U1.14, U1.45, U1.49; also elsewhere on the board
unnamed: C2.1, U1.42
unnamed: C2.2, U1.43
unnamed: C3.1, U1.15
unnamed: C4.1, U1.40
unnamed: C4.2, U1.39
unnamed: C5.1, U1.46
unnamed: C19.2, U1.38
unnamed: C20.1, U1.37
unnamed: D1.1 (K), R7.1
unnamed: D2.1 (K), R10.1
unnamed: R2.2, U1.44

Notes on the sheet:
Aluminum Polymer Bulk Capacitance
Ceramic High Frequency Decoupling
H-Bridges and VIN
External Signals
DRV8305
Test different cap values, try to minimize cap size and cost!



Board: 4 copper layers, 108.0 x 54.0 mm, 163 parts (33 on the bottom side), 92 nets.

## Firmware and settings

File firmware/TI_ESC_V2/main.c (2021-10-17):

//#############################################################################
// $TI Release: MotorControl SDK v3.00.01.00 $
// $Release Date: Tue May 26 19:13:59 CDT 2020 $
// $Copyright:
// Copyright (C) 2017-2018 Texas Instruments Incorporated - http://www.ti.com/
//
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
//   Redistributions of source code must retain the above copyright
//   notice, this list of conditions and the following disclaimer.
//
//   Redistributions in binary form must reproduce the above copyright
//   notice, this list of conditions and the following disclaimer in the
//   documentation and/or other materials provided with the
//   distribution.
//
//   Neither the name of Texas Instruments Incorporated nor the names of
//   its contributors may be used to endorse or promote products derived
//   from this software without specific prior written permission.
//
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
//| Modified from lab8 from TI's InstaSPIN FOC MotorControl SDK
//| Other modifications are found throughout project files
//|
//| For The TMS320F2800041C and DRV8320
//| And use with the custom motor controller
//| for the T200 UUV thruster
//|
//| Mark Belbin -- Feb 2021

// **************************************************************************

#include "labs.h"

#pragma CODE_SECTION(mainISR, ".TI.ramfunc");

//
// the globals
//

#define CAN_TELEM_FREQ_Hz  (10.0)     // 10 Hz
#define RPM_RESET_FREQ_Hz  (0.2)     // 0.2 Hz, 5 seconds

uint16_t rxMsgData[3]; // Placeholder for recieved data, maximum of three bytes
uint16_t rpmMsgData[3];
uint16_t voltageData[2];
uint16_t torqueData[2];
uint16_t faults[2];
uint16_t boardState[1];

bool RPMset = false;

//***********************

HAL_ADCData_t adcData = {{0.0, 0.0, 0.0}, {0.0, 0.0, 0.0}, 0.0};

HAL_PWMData_t pwmData = {{0.0, 0.0, 0.0}};

uint16_t counterLED = 0;  //!< Counter used to divide down the ISR rate for
                           //!< visually blinking an LED

uint16_t counterCAN = 0; // Counter used to determine when to send CAN telemetry
uint32_t counterRPM = 0; // Counter to check if RPM signals are not being recieved

uint16_t counterSpeed = 0;
uint16_t counterTrajSpeed = 0;
uint16_t counterTrajId = 0;

uint32_t offsetCalcCount = 0;     //!< Counter used to count the wait time
                                  //!< for offset calibration, unit: ISR cycles

uint32_t offsetCalcWaitTime = 50000;  //!< Wait time setting for current/voltage
                                      //!< offset calibration, unit: ISR cycles

EST_InputData_t estInputData = {0, {0.0, 0.0}, {0.0, 0.0}, 0.0, 0.0};

EST_OutputData_t estOutputData = {0, 0.0, 0.0, 0.0, 0.0, 0.0, 0.0,
                                  {0.0, 0.0}, {0.0, 0.0}, 0, 0.0};
float32_t angleDelta_rad;   //!< the rotor angle compensation value
float32_t angleEst_rad;     //!< the rotor angle from FAST estimator
float32_t angleGen_rad;     //!< the rotor angle from rampgen module
float32_t angleFoc_rad;     //!< the rotor angle for FOC modules

MATH_Vec2 Idq_ref_A;        //!< the reference current on d&q rotation axis
MATH_Vec2 Idq_offset_A;     //!< the offsetting current on d&q rotation axis
MATH_Vec2 Iab_in_A;         //!< the alpha&beta axis current are converter from
                            //!< 3-phase sampling input current of motor
MATH_Vec2 Idq_in_A;         //!< the d&q axis current are converter from
                            //!< 3-phase sampling input current of motor
MATH_Vec2 Vab_out_V;        //!< the output control voltage on alpha&beta axis
MATH_Vec2 Vdq_out_V;        //!< the output control voltage on d&q axis

USER_Params userParams;    //!< the user parameters for motor control
                            //!< and hardware board configuration
#pragma DATA_SECTION(userParams, "ctrl_data");

volatile MOTOR_Vars_t motorVars = MOTOR_VARS_INIT;
#pragma DATA_SECTION(motorVars, "ctrl_data");

CTRL_Handle   ctrlHandle;       //!< the handle for the controller
CTRL_Obj      ctrl;             //!< the controller object

CLARKE_Handle clarkeHandle_I;   //!< the handle for the current Clarke transform
CLARKE_Obj    clarke_I;         //!< the current Clarke transform object

CLARKE_Handle clarkeHandle_V;   //!< the handle for the voltage Clarke transform
CLARKE_Obj    clarke_V;         //!< the voltage Clarke transform object

EST_Handle    estHandle;        //!< the handle for the estimator

HAL_Handle    halHandle;     //!< the handle for the hardware abstraction layer
HAL_Obj       hal;           //!< the hardware abstraction layer object

IPARK_Handle  iparkHandle;      //!< the handle for the inverse Park transform
IPARK_Obj     ipark;            //!< the inverse Park transform object

PARK_Handle   parkHandle;       //!< the handle for the Park object
PARK_Obj      park;             //!< the Park transform object

PI_Handle     piHandle_Id;      //!< the handle for the Id PI controller
PI_Obj        pi_Id;            //!< the Id PI controller object

PI_Handle     piHandle_Iq;      //!< the handle for the Iq PI controller
PI_Obj        pi_Iq;            //!< the Iq PI controller object

PI_Handle     piHandle_fwc;     //!< the handle for the Iq PI controller
PI_Obj        pi_fwc;           //!< the Iq PI controller object

PI_Handle     piHandle_spd;     //!< the handle for the speed PI controller
PI_Obj        pi_spd;           //!< the speed PI controller object

SVGEN_Handle  svgenHandle;      //!< the handle for the space vector generator
SVGEN_Obj     svgen;            //!< the space vector generator object

SVGENCURRENT_Obj svgencurrent;              //!< the handle for the space vector
                                            //!< generator current
SVGENCURRENT_Handle svgencurrentHandle;     //!< the space vector generator
                                            //!< current object

TRAJ_Handle   trajHandle_spd; //!< the handle for the speed reference trajectory
TRAJ_Obj      traj_spd;       //!< the speed reference trajectory object

TRAJ_Handle   trajHandle_Id;    //!< the handle for the id reference trajectory
TRAJ_Obj      traj_Id;          //!< the id reference trajectory object

TRAJ_Handle   trajHandle_fwc;   //!< the handle for the id reference trajectory
TRAJ_Obj      traj_fwc;         //!< the id reference trajectory object

//!< the handles for the current offset calculation
FILTER_FO_Handle  filterHandle_I[USER_NUM_CURRENT_SENSORS];
//!< the current offset calculation
FILTER_FO_Obj     filter_I[USER_NUM_CURRENT_SENSORS];

//
// the handles for the voltage offset calculation
//
FILTER_FO_Handle  filterHandle_V[USER_NUM_VOLTAGE_SENSORS];

//
// the voltage offset calculation
//
FILTER_FO_Obj     filter_V[USER_NUM_VOLTAGE_SENSORS];

SVGENCURRENT_MeasureShunt_e measurableShuntThisCycle = SVGENCURRENT_ALL_PHASE_MEASURABLE;
SVGENCURRENT_IgnoreShunt_e ignoreShuntNextCycle = SVGENCURRENT_USE_ALL;
SVGENCURRENT_VmidShunt_e midVolShunt = SVGENCURRENT_VMID_A;

//
//  set the offset, default value of 1 microsecond
//
int16_t cmpOffset = (int16_t)(1.0 * USER_SYSTEM_FREQ_MHz);

MATH_Vec3 adcDataPrev = {0.0, 0.0, 0.0};
MATH_Vec3 pwmDataPrev = {0.0, 0.0, 0.0};

#ifdef DRV8320_SPI
//
// Watch window interface to the 8320 SPI
//
DRV8320_SPIVars_t drvSPI8320Vars;
#pragma DATA_SECTION(drvSPI8320Vars, "ctrl_data");
#endif

//
// the functions
//

void main(void)
{
    uint16_t estNumber = 0;
    bool flagEstStateChanged = false;

    // Global board state
    boardState[0] = 0x00;

    // Define board used
    motorVars.boardKit = BOARD_T200_CONTROLLER;

    //************************************

    //
    // initialize the user parameters
    //
    USER_setParams(&userParams);

    userParams.flag_bypassMotorId = true;

    motorVars.flagEnableOffsetCalc = true;

    motorVars.Kp_spd = 0.2; // Set Kp and Ki values for speed controller.
    motorVars.Ki_spd = 0.001;

    //
    // initialize the user parameters
    //
    USER_setParams_priv(&userParams);

    //
    // initialize the driver
    //
    halHandle = HAL_init(&hal, sizeof(hal));

    //
    // set the driver parameters
    //
    HAL_setParams(halHandle);

    //
    // initialize the Clarke modules
    //
    clarkeHandle_I = CLARKE_init(&clarke_I, sizeof(clarke_I));
    clarkeHandle_V = CLARKE_init(&clarke_V, sizeof(clarke_V));

    //
    // set the Clarke parameters
    //
    setupClarke_I(clarkeHandle_I, userParams.numCurrentSensors);
    setupClarke_V(clarkeHandle_V, userParams.numVoltageSensors);

    //
    // initialize the estimator
    //
    estHandle = EST_initEst(estNumber);

    //
    // set the default estimator parameters
    //
    EST_setParams(estHandle, &userParams);
    EST_setFlag_enableForceAngle(estHandle, motorVars.flagEnableForceAngle);
    EST_setFlag_enableRsRecalc(estHandle, motorVars.flagEnableRsRecalc);

    //
    // initialize the inverse Park module
    //
    iparkHandle = IPARK_init(&ipark, sizeof(ipark));

    //
    // initialize the Park module
    //
    parkHandle = PARK_init(&park, sizeof(park));

    //
    // initialize the PI controllers
    //
    piHandle_Id  = PI_init(&pi_Id, sizeof(pi_Id));
    piHandle_Iq  = PI_init(&pi_Iq, sizeof(pi_Iq));
    piHandle_fwc = PI_init(&pi_fwc, sizeof(pi_fwc));
    piHandle_spd = PI_init(&pi_spd, sizeof(pi_spd));

    //
    // setup the controllers, speed, d/q-axis current pid regulator
    //
    setupControllers();

    //
    // initialize the space vector generator module
    //
    svgenHandle = SVGEN_init(&svgen, sizeof(svgen));

    //
    // Initialize and setup the 100% SVM generator
    //
    svgencurrentHandle = SVGENCURRENT_init(&svgencurrent, sizeof(svgencurrent));

    //
    // setup svgencurrent for over modulation function
    //
    {
        float32_t minWidth_usec = 2.0;  // set minimum pwm width to 2.0us

        uint16_t minWidth_counts =
                (uint16_t)(minWidth_usec * USER_SYSTEM_FREQ_MHz);

        //
        // maximum output voltage duty: 0.5
        // convert the minimum pwm width to duty by divide Tpwm
        // Tpwm = 1/(USER_PWM_FREQ_kHz * 1000) = * (USER_PWM_FREQ_kHz * 0.001)
        // The minimum pwm width is the same in two zero vectors for svpwm
        float32_t dutyLimit =
                0.5 - (2.0 * minWidth_usec * USER_PWM_FREQ_kHz * 0.001);

        SVGENCURRENT_setMinWidth(svgencurrentHandle, minWidth_counts);
        SVGENCURRENT_setIgnoreShunt(svgencurrentHandle, SVGENCURRENT_USE_ALL);
        SVGENCURRENT_setMode(svgencurrentHandle, SVGENCURRENT_ALL_PHASE_MEASURABLE);
        SVGENCURRENT_setVlimit(svgencurrentHandle, dutyLimit);
    }

    //
    // initialize the speed reference trajectory
    //
    trajHandle_spd = TRAJ_init(&traj_spd, sizeof(traj_spd));

    //
    // configure the speed reference trajectory (Hz)
    //
    TRAJ_setTargetValue(trajHandle_spd, 0.0);
    TRAJ_setIntValue(trajHandle_spd, 0.0);
    TRAJ_setMinValue(trajHandle_spd, -USER_MOTOR_FREQ_MAX_HZ);
    TRAJ_setMaxValue(trajHandle_spd, USER_MOTOR_FREQ_MAX_HZ);
    TRAJ_setMaxDelta(trajHandle_spd, (USER_MAX_ACCEL_Hzps / USER_ISR_FREQ_Hz));

    //
    // initialize the Id reference trajectory
    //
    trajHandle_Id = TRAJ_init(&traj_Id, sizeof(traj_Id));

    //
    // configure the Id reference trajectory
    //
    TRAJ_setTargetValue(trajHandle_Id, 0.0);
    TRAJ_setIntValue(trajHandle_Id, 0.0);
    TRAJ_setMinValue(trajHandle_Id, -USER_MOTOR_MAX_CURRENT_A);
    TRAJ_setMaxValue(trajHandle_Id,  USER_MOTOR_MAX_CURRENT_A);
    TRAJ_setMaxDelta(trajHandle_Id,
                     (USER_MOTOR_RES_EST_CURRENT_A / USER_ISR_FREQ_Hz));

    //
    // initialize the fwc reference trajectory
    //
    trajHandle_fwc = TRAJ_init(&traj_fwc, sizeof(traj_fwc));

    //
    // configure the fwc reference trajectory
    //
    TRAJ_setTargetValue(trajHandle_fwc, 0.0);
    TRAJ_setIntValue(trajHandle_fwc, 0.0);
    TRAJ_setMinValue(trajHandle_fwc, -USER_MOTOR_MAX_CURRENT_A);
    TRAJ_setMaxValue(trajHandle_fwc,  USER_MOTOR_MAX_CURRENT_A);
    TRAJ_setMaxDelta(trajHandle_fwc,
                     (USER_MOTOR_RES_EST_CURRENT_A / USER_ISR_FREQ_Hz));

    //
    // initialize and configure offsets using first-order filter
    //
    {
        //
        // Sets the first-order filter denominator coefficients
        // a1, the filter coefficient value for z^(-1)
        // b0, the filter coefficient value for z^0
        // b1, the filter coefficient value for z^(-1)
        //
        uint16_t cnt = 0;
        float32_t b0 = userParams.offsetPole_rps / userParams.ctrlFreq_Hz;
        float32_t a1 = (b0 - 1.0);
        float32_t b1 = 0.0;

        //
        // For Current offset calibration filter
        //
        for(cnt = 0; cnt < USER_NUM_CURRENT_SENSORS; cnt++)
        {
            filterHandle_I[cnt] = FILTER_FO_init(&filter_I[cnt],
                                                   sizeof(filter_I[cnt]));

            FILTER_FO_setDenCoeffs(filterHandle_I[cnt], a1);
            FILTER_FO_setNumCoeffs(filterHandle_I[cnt], b0, b1);

            FILTER_FO_setInitialConditions(filterHandle_I[cnt],
                                        motorVars.offsets_I_A.value[cnt],
                                        motorVars.offsets_I_A.value[cnt]);
        }

        //
        // For Voltage offset calibration filter
        //
        for(cnt = 0; cnt < USER_NUM_VOLTAGE_SENSORS; cnt++)
        {
            filterHandle_V[cnt] = FILTER_FO_init(&filter_V[cnt],
                                                   sizeof(filter_V[cnt]));

            FILTER_FO_setDenCoeffs(filterHandle_V[cnt], a1);
            FILTER_FO_setNumCoeffs(filterHandle_V[cnt], b0, b1);

            FILTER_FO_setInitialConditions(filterHandle_V[cnt],
                                        motorVars.offsets_V_V.value[cnt],
                                        motorVars.offsets_V_V.value[cnt]);
        }

        motorVars.flagEnableOffsetCalc = true;
        offsetCalcCount = 0;
    }

    motorVars.offset_invVbus_invV = 0.5;   // the scale factor of half of dc bus

    motorVars.faultMask.all = FAULT_MASK_ALL_FLTS;

    //
    // setup faults
    //
    //HAL_setupFaults(halHandle); // NOT SETTING FAULTS DUE TO CMPSS tripping incorrectly at 1.5A

    //
    // setup OVM PWM
    //
    HAL_setOvmParams(halHandle, &pwmData);

    //
    // turn on the DRV8320 if present
    //
    HAL_enableDRV(halHandle);

    //
    // initialize the DRV8320 interface
    //
    HAL_setupDRVSPI(halHandle, &drvSPI8320Vars);

    drvSPI8320Vars.Ctrl_Reg_05.VDS_LVL = DRV8320_VDS_LEVEL_1P300_V;
    drvSPI8320Vars.Ctrl_Reg_05.DEAD_TIME = DRV8320_DEADTIME_100_NS;
    drvSPI8320Vars.writeCmd = 1;

    //
    // Set some global variables
    //
    motorVars.pwmISRCount = 0;          // Clear the counter
    motorVars.speedRef_Hz = 0.0;      // Set reference frequency to 0 Hz
    motorVars.flagEnableForceAngle = 0; // Disable ForceAngle
    motorVars.accelerationMax_Hzps = 500; // Set initial accel to 500 (Max is 1000)

    //
    // disable the PWM
    //
    HAL_disablePWM(halHandle);

    //
    // initialize the interrupt vector table
    //
    HAL_initIntVectorTable(halHandle);

    //
    // enable the ADC interrupts
    //
    HAL_enableADCInts(halHandle);

    //
    // disable global interrupts
    //
    HAL_enableGlobalInts(halHandle);

    //
    // enable debug interrupts
    //
    HAL_enableDebugInt(halHandle);

    //
    // Waiting for enable system flag to be set
    //
    while(motorVars.flagEnableSys == false)
    {

    }

    //
    // loop while the enable system flag is true
    //
    while(motorVars.flagEnableSys == true)
    {
        //
        // 1ms time base
        //
        if(HAL_getTimerStatus(halHandle, HAL_CPU_TIMER1))
        {
            motorVars.timerCnt_1ms++;

            HAL_clearTimerFlag(halHandle, HAL_CPU_TIMER1);
        }

        motorVars.mainLoopCount++;

        //
        // set the reference value for internal DACA and DACB
        //
        HAL_setDACValue(halHandle, 0, motorVars.dacaVal);
        HAL_setDACValue(halHandle, 1, motorVars.dacbVal);

        //
        // set internal DAC value for on-chip comparator for current protection
        //
        {
            uint16_t  cmpssCnt;

            for(cmpssCnt = 0; cmpssCnt < HAL_NUM_CMPSS_CURRENT; cmpssCnt++)
            {
                HAL_setCMPSSDACValueHigh(halHandle,
                                         cmpssCnt, motorVars.dacValH);

                HAL_setCMPSSDACValueLow(halHandle,
                                        cmpssCnt, motorVars.dacValL);
            }
        }

        //
        // enable or disable force angle
        //
        EST_setFlag_enableForceAngle(estHandle,
                                     motorVars.flagEnableForceAngle);


        if(HAL_getPwmEnableStatus(halHandle) == true)
        {
            if(HAL_getTripFaults(halHandle) != 0)
            {
                motorVars.faultNow.bit.moduleOverCurrent = 1;
            }
        }

        motorVars.faultUse.all =
                motorVars.faultNow.all & motorVars.faultMask.all;

        //
        // Had some faults to stop the motor
        //
        if(motorVars.faultUse.all != 0)
        {
            motorVars.flagRunIdentAndOnLine = false;
            motorVars.flagEnableRunAndIdentify = false;
        }

        if((motorVars.flagRunIdentAndOnLine == true) &&
           (motorVars.flagEnableOffsetCalc == false))
        {
            if(HAL_getPwmEnableStatus(halHandle) == false)
            {
                //
                // enable the estimator
                //
                EST_enable(estHandle);

                //
                // enable the trajectory generator
                //
                EST_enableTraj(estHandle);

                //
                // enable the PWM
                //
                HAL_enablePWM(halHandle);
            }

            //
            // set the reference to the trajectory of speed
            //
            TRAJ_setTargetValue(trajHandle_spd, motorVars.speedRef_Hz);

            //
            // set the acceleration to the trajectory of speed
            //
            TRAJ_setMaxDelta(trajHandle_spd,
                           (motorVars.accelerationMax_Hzps / USER_ISR_FREQ_Hz));
        }
        else if(motorVars.flagEnableOffsetCalc == false)
        {
            //
            // disable the estimator
            //
            EST_disable(estHandle);

            //
            // disable the trajectory generator
            //
            EST_disableTraj(estHandle);

            //
            // disable the PWM
            //
            HAL_disablePWM(halHandle);

            //
            // clear integral outputs of the controllers
            //
            PI_setUi(piHandle_Id, 0.0);
            PI_setUi(piHandle_Iq, 0.0);
            PI_setUi(piHandle_fwc, 0.0);
            PI_setUi(piHandle_spd, 0.0);

            //
            // clear current references
            //
            Idq_ref_A.value[0] = 0.0;
            Idq_ref_A.value[1] = 0.0;

            //
            // clear current offsets
            //
            Idq_offset_A.value[0] = 0.0;
            Idq_offset_A.value[1] = 0.0;

            //
            // get the magnetic current for ACIM
            //
            motorVars.IdRated_A = EST_getIdRated_A(estHandle);

            //
            // clear current and angle for FWC and MTPA
            //
            motorVars.VsRef_pu = USER_MAX_VS_MAG_PU;
            motorVars.IsRef_A = 0.0;
            motorVars.angleCurrent_rad = 0.0;

            //
            // clear the trajectory of speed
            //
            TRAJ_setTargetValue(trajHandle_spd, 0.0);
            TRAJ_setIntValue(trajHandle_spd, 0.0);
        }

        //
        // check the trajectory generator
        //
        if(EST_isTrajError(estHandle) == true)
        {
            //
            // disable the PWM
            //
            HAL_disablePWM(halHandle);

            //
            // set the enable system flag to false
            //
            motorVars.flagEnableSys = false;
        }
        else
        {
            //
            // update the trajectory generator state
            //
            EST_updateTrajState(estHandle);
        }

        //
        // check the estimator
        //
        if(EST_isError(estHandle) == true)
        {
            //
            // disable the PWM
            //
            HAL_disablePWM(halHandle);

            //
            // set the enable system flag to false
            //
            motorVars.flagEnableSys = false;
        }
        else        // No estimator error
        {
            motorVars.Id_target_A = EST_getIntValue_Id_A(estHandle);

            flagEstStateChanged = EST_updateState(estHandle, 0.0);

            if(flagEstStateChanged == true)
            {
                //
                // configure the trajectory generator
                //
                EST_configureTraj(estHandle);
            }
        }

        if(EST_isMotorIdentified(estHandle) == true)
        {
            if(motorVars.flagSetupController == true)
            {
                //
                // update the controller
                // set custom current and speed controllers gains
                //
                updateControllers();
            }
            else
            {
                motorVars.flagMotorIdentified = true;
                motorVars.flagSetupController = true;

                setupControllers();
            }
        }
        //
        // update the global variables
        //
        updateGlobalVariables(estHandle);

        //
        // DRV8320 Read/Write
        //
        HAL_writeDRVData(halHandle, &drvSPI8320Vars);

        HAL_readDRVData(halHandle, &drvSPI8320Vars);

    } // end of while() loop

    //
    // disable the PWM
    //
    HAL_disablePWM(halHandle);

} // end of main() function
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

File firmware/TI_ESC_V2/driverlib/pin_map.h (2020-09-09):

//###########################################################################
//
// FILE:   pin_map.h
//
// TITLE:  Definitions of pin mux info for gpio.c.
//
//###########################################################################
// $TI Release: F28004x Support Library v1.10.00.00 $
// $Release Date: Tue May 26 17:06:03 IST 2020 $
// $Copyright:
// Copyright (C) 2020 Texas Instruments Incorporated - http://www.ti.com/
//
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
//   Redistributions of source code must retain the above copyright 
//   notice, this list of conditions and the following disclaimer.
// 
//   Redistributions in binary form must reproduce the above copyright
//   notice, this list of conditions and the following disclaimer in the 
//   documentation and/or other materials provided with the   
//   distribution.
// 
//   Neither the name of Texas Instruments Incorporated nor the names of
//   its contributors may be used to endorse or promote products derived
//   from this software without specific prior written permission.
// 
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
#ifndef PIN_MAP_H
#define PIN_MAP_H
                                                                               
//*****************************************************************************
// 0x00000003 = MUX register value                                             
// 0x0000000C = GMUX register value                                            
// 0x0000FF00 = Shift amount within mux registers                              
// 0xFFFF0000 = Offset of MUX register                                         
//*****************************************************************************

//*****************************************************************************
// Latest pinmuxing MACROS - Recommended for new users                         
//*****************************************************************************
#define GPIO_0_GPIO0                    0x00060000U
#define GPIO_0_EPWM1_A                  0x00060001U
#define GPIO_0_I2CA_SDA                 0x00060006U

#define GPIO_1_GPIO1                    0x00060200U
#define GPIO_1_EPWM1_B                  0x00060201U
#define GPIO_1_I2CA_SCL                 0x00060206U

#define GPIO_2_GPIO2                    0x00060400U
#define GPIO_2_EPWM2_A                  0x00060401U
#define GPIO_2_OUTPUTXBAR1              0x00060405U
#define GPIO_2_PMBUSA_SDA               0x00060406U
#define GPIO_2_SCIA_TX                  0x00060409U
#define GPIO_2_FSIRXA_D1                0x0006040AU

#define GPIO_3_GPIO3                    0x00060600U
#define GPIO_3_EPWM2_B                  0x00060601U
#define GPIO_3_OUTPUTXBAR2              0x00060602U
#define GPIO_3_PMBUSA_SCL               0x00060606U
#define GPIO_3_SPIA_CLK                 0x00060607U
#define GPIO_3_SCIA_RX                  0x00060609U
#define GPIO_3_FSIRXA_D0                0x0006060AU

#define GPIO_4_GPIO4                    0x00060800U
#define GPIO_4_EPWM3_A                  0x00060801U
#define GPIO_4_OUTPUTXBAR3              0x00060805U
#define GPIO_4_CANA_TX                  0x00060806U
#define GPIO_4_FSIRXA_CLK               0x0006080AU

#define GPIO_5_GPIO5                    0x00060A00U
#define GPIO_5_EPWM3_B                  0x00060A01U
#define GPIO_5_OUTPUTXBAR3              0x00060A03U
#define GPIO_5_CANA_RX                  0x00060A06U
#define GPIO_5_SPIA_STE                 0x00060A07U
#define GPIO_5_FSITXA_D1                0x00060A09U

#define GPIO_6_GPIO6                    0x00060C00U
#define GPIO_6_EPWM4_A                  0x00060C01U
#define GPIO_6_OUTPUTXBAR4              0x00060C02U
#define GPIO_6_SYNCOUT                  0x00060C03U
#define GPIO_6_EQEP1_A                  0x00060C05U
#define GPIO_6_CANB_TX                  0x00060C06U
#define GPIO_6_SPIB_SOMI                0x00060C07U
#define GPIO_6_FSITXA_D0                0x00060C09U

#define GPIO_7_GPIO7                    0x00060E00U
#define GPIO_7_EPWM4_B                  0x00060E01U
#define GPIO_7_OUTPUTXBAR5              0x00060E03U
#define GPIO_7_EQEP1_B                  0x00060E05U
#define GPIO_7_CANB_RX                  0x00060E06U
#define GPIO_7_SPIB_SIMO                0x00060E07U
#define GPIO_7_FSITXA_CLK               0x00060E09U

#define GPIO_8_GPIO8                    0x00061000U
#define GPIO_8_EPWM5_A                  0x00061001U
#define GPIO_8_CANB_TX                  0x00061002U
#define GPIO_8_ADCSOCAO                 0x00061003U
#define GPIO_8_EQEP1_STROBE             0x00061005U
#define GPIO_8_SCIA_TX                  0x00061006U
#define GPIO_8_SPIA_SIMO                0x00061007U
#define GPIO_8_I2CA_SCL                 0x00061009U
#define GPIO_8_FSITXA_D1                0x0006100AU
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

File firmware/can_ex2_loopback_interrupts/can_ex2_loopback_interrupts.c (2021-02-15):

//#############################################################################
//
// FILE:   can_ex2_loopback_interrupts.c
//
// TITLE:   CAN External Loopback with Interrupts Example
//
//! \addtogroup driver_example_list
//! <h1> CAN External Loopback with Interrupts </h1>
//!
//! This example shows the basic setup of CAN in order to transmit and receive
//! messages on the CAN bus.  The CAN peripheral is configured to transmit
//! messages with a specific CAN ID.  A message is then transmitted once per
//! second, using a simple delay loop for timing.  The message that is sent is
//! a 4 byte message that contains an incrementing pattern.  A CAN interrupt
//! handler is used to confirm message transmission and count the number of
//! messages that have been sent.
//!
//! This example sets up the CAN controller in External Loopback test mode.
//! Data transmitted is visible on the CANTXA/CANATX pin and is received internally
//! back to the CAN Core.
//!
//! \b External \b Connections \n
//!  - None.
//!
//! \b Watch \b Variables \n
//!  - txMsgCount - A counter for the number of messages sent
//!  - rxMsgCount - A counter for the number of messages received
//!  - txMsgData - An array with the data being sent
//!  - rxMsgData - An array with the data that was received
//!  - errorFlag - A flag that indicates an error has occurred
//!
//
//#############################################################################
// $TI Release: F28004x Support Library v1.11.00.00 $
// $Release Date: Sun Oct  4 15:49:15 IST 2020 $
// $Copyright:
// Copyright (C) 2020 Texas Instruments Incorporated - http://www.ti.com/
//
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
//   Redistributions of source code must retain the above copyright 
//   notice, this list of conditions and the following disclaimer.
// 
//   Redistributions in binary form must reproduce the above copyright
//   notice, this list of conditions and the following disclaimer in the 
//   documentation and/or other materials provided with the   
//   distribution.
// 
//   Neither the name of Texas Instruments Incorporated nor the names of
//   its contributors may be used to endorse or promote products derived
//   from this software without specific prior written permission.
// 
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
//
// Included Files
//
#include "driverlib.h"
#include "device.h"

//
// Defines
//
#define MSG_DATA_LENGTH    4
#define TX_MSG_OBJ_ID      1
#define RX_MSG_OBJ_ID      2

//
// Globals
//
volatile uint32_t txMsgCount = 0;
volatile uint32_t rxMsgCount = 0;
volatile uint32_t errorFlag = 0;
uint16_t txMsgData[4];
uint16_t rxMsgData[4];

//
// Function Prototypes
//
__interrupt void canISR(void);

//
// Main
//
void main(void)
{
    //
    // Initialize device clock and peripherals
    //
    Device_init();

    //
    // Initialize GPIO and configure GPIO pins for CANTX/CANRX
    //
    Device_initGPIO();
    GPIO_setPinConfig(DEVICE_GPIO_CFG_CANRXA);
    GPIO_setPinConfig(DEVICE_GPIO_CFG_CANTXA);

    //
    // Initialize the CAN controller
    //
    CAN_initModule(CANA_BASE);

    //
    // Set up the CAN bus bit rate to 500kHz
    // Refer to the Driver Library User Guide for information on how to set
    // tighter timing control. Additionally, consult the device data sheet
    // for more information about the CAN module clocking.
    //
    CAN_setBitRate(CANA_BASE, DEVICE_SYSCLK_FREQ, 500000, 20);

    //
    // Enable interrupts on the CAN peripheral.
    //
    CAN_enableInterrupt(CANA_BASE, CAN_INT_IE0 | CAN_INT_ERROR |
                        CAN_INT_STATUS);

    //
    // Initialize PIE and clear PIE registers. Disables CPU interrupts.
    //
    Interrupt_initModule();

    //
    // Initialize the PIE vector table with pointers to the shell Interrupt
    // Service Routines (ISR).
    //
    Interrupt_initVectorTable();

    //
    // Enable Global Interrupt (INTM) and realtime interrupt (DBGM)
    //
    EINT;
    ERTM;

    //
    // Interrupts that are used in this example are re-mapped to
    // ISR functions found within this file.
    // This registers the interrupt handler in PIE vector table.
    //
    Interrupt_register(INT_CANA0, &canISR);

    //
    // Enable the CAN interrupt signal
    //
    Interrupt_enable(INT_CANA0);
    CAN_enableGlobalInterrupt(CANA_BASE, CAN_GLOBAL_INT_CANINT0);

    //
    // Enable CAN test mode with external loopback
    //
    CAN_enableTestMode(CANA_BASE, CAN_TEST_EXL);

    //
    // Initialize the transmit message object used for sending CAN messages.
    // Message Object Parameters:
    //      Message Object ID Number: 1
    //      Message Identifier: 0x1
    //      Message Frame: Standard
    //      Message Type: Transmit
    //      Message ID Mask: 0x0
    //      Message Object Flags: Transmit Interrupt
    //      Message Data Length: 4 Bytes
    //
    CAN_setupMessageObject(CANA_BASE, TX_MSG_OBJ_ID, 0x1, CAN_MSG_FRAME_STD,
                           CAN_MSG_OBJ_TYPE_TX, 0, CAN_MSG_OBJ_TX_INT_ENABLE,
                           MSG_DATA_LENGTH);
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

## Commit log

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2020-01-14 Schematic Complete
    - Completed Full Schematic
    - Completed BOM
    - Some footprints selected
    [XDS100v2 Programmer.csv, XDS100v2 Programmer.sch]
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2020-01-14 Schematic Update
    - Fixed small schematic issues (resistors in the wrong place)
    - Add thermal pad to FTDI chip symbol
    [XDS100v2 Programmer.sch]
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2020-01-15 Changed Output Pinout
    - Changed programming cable connector to follow ARM 10 Pin JTAG standard, although it is slightly modified.
    [XDS100v2 Programmer.sch]
2020-01-15 Removed Pulldown
    - Removed pulldown on TRST line
    - Will be permanently added to the main test board or integrated board.
    - If programmer is not plugged in, the board will automatically boot to flash. If connected, the option is there to connect the TRST pin to JTAGTRST for JTAG debugging, while still enabling boot from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
    [XDS100v2 Programmer.sch]
2020-01-16 Schematic Changes
    - Added TI MCU Symbol
    - Added Powertrain V1 schematic
    - Setup Hierarcical Sheets
    [ESC Drivetrain V1.sch, MCU_Powertrain.sch, Powertrain.sch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]
2020-01-16 Updated TI_MCU Sheet
    -Added all required components onto the TI-MCU sheet other than the external connections (header pins on the dev board)
    - Added pulldown and pullup resistors for proper JTAG debug and flashing functionality.
    [TI_MCU.sch]
2020-01-19 More Schematic Changes
    - Connected TI_MCU schematic to Powertrain schematic
    - Added power input
    [MCU_Powertrain.sch, Powertrain.sch, TI_MCU.sch]
2020-01-19 Removed Unused Pins
    - GPIO34 and TDO switch options are useless for this application, removed them to reduce complexity.
    - Updated programming pin interface
    [XDS100v2 Programmer.sch]
2020-01-19 Added Programming Headers
    - Inserted programming headers based on latest header format from custom XDS100v2 programmer.
    [MCU_Powertrain.sch, TI_MCU.sch]
2020-01-19 CAN and Minor Changes
    - Added CAN Controller (MCP2515) and CAN transciever
    - Added net-ties to shunts
    - Removed all +12V references and replaced with +BATT references.
    [MCU_Powertrain.sch, Powertrain.sch, TI_MCU.sch]
2020-01-20 TI_MCU Updates
    - Connected GPIO12 to CAN_INT, made switch active low so that it can test the interrupt.
    - Connected SPI CS_1 to GPIO32
    [MCU_Powertrain.sch, Powertrain.sch, TI_MCU.sch]
2020-01-20 Testpoints
    - Added Testpoints everywhere!
    - Schematic is "done" and any mistakes should be able to be corrected with small bodges later
    [MCU_Powertrain.sch, TI_MCU.sch]
2020-01-21 Completed BOM
    - Added Digikey PNs to each component.
    - Removed double 3V3 LED indicator
    [MCU_Powertrain.csv, MCU_Powertrain.sch, Powertrain.sch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]
2020-01-22 Assigned Footprints
    - All footprints assigned
    - Created RA 3mm bullet fooprint, may need to adjust it later
    - Fixed errors
    [3020-10-0100-xx.SLDPRT, 3020-10-0100-xx.STEP, 3020-10-0100-xx.igs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]
2020-01-22 Small Tweaks
    - Removed double CAN int pullup
    - Double checked overall schematic
    [MCU_Powertrain.kicad_pcb, MCU_Powertrain.sch, TI_MCU.sch]
2020-01-23 Complete Schematic
    - Completed initial schematic
    - Lots of test points
    - Some footprints and BOM selected
    [Power Sense PCB.sch]
2020-01-23 Schematic + BOM
    - Added 0.1uF decoupling caps
    - Added resistor division, same as DRV8305 eval board
    - Spec'd more of the BOM
    [5x6mm FET.SLDPRT, 5x6mm FET.STEP, BulletA.SLDPRT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]
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2020-01-24 Layout + Routing
    - Added 5V LED indicatior
    - Added 330uF bulk cap on 5V rail
    - Changed 8pin to 9pin header (added ground)
    - Completed all layout and routing!
    [CUI_DEVICES_PJ-002A.step, Power Sense PCB.kicad_pcb, Power Sense PCB.sch]
2020-01-25 Gerbers and Small Changes
    - Swapped Ref1 and Ref2 values based on datasheet (doesn't matter really)
    - Updated Silkscreen
    - Exported Gerbers
    [Power Sense PCB-B_Cu.gbl, Power Sense PCB-B_Mask.gbs, Power Sense PCB-B_SilkS.gbo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]
2020-01-27 Layout + Routing
    - Completed initial layout and routing, board is defined mechanically.
    [3020-10-0100-xx.STEP]
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2020-01-27 3D Models + Gerbers
    - Updated all 3D models
    - Generated Gerbers
    [204-2 (1).SLDASM, 204-2.STEP, 204-3.SLDASM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]
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2020-01-28 Schematic + Footprints + BOM
    - Completed schematic
    - Assigned footprints
    - Updated BOM
    [RPM Sensor.sch]
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2020-01-29 Initial Layout, 3D Models, 0402s
    - Changed C2, C4, C9, C16, C18 to 0402
    - Some intial layout
    - All 3D models added
    [3pinRA.STEP, 705530002.SLDPRT, 705530002.STEP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]
2020-01-30 More Layout + Schematic
    - Fixed small issue with net labels, ISEN labels were not seperated on the DRV sheet.
    - More layout
    [MCU_Powertrain.kicad_pcb, Powertrain.sch, TI_MCU.sch]
2020-01-30 Initial Layout
    - Full initial layout complete, can probably shrink the board further as routing is complete
    [MCU_Powertrain.kicad_pcb, TI_MCU.sch]
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2020-02-06 Routing
    - Routed most of DRV and TI chips
    - FETs are done
    - Added board outline
    - Added power and ground planes
    [MCU_Powertrain.kicad_pcb, MCU_Powertrain.sch, TI_MCU.sch]
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2020-02-07 Initial Routing Complete
    - Connected all nets, no DRC errors
    - Still need to investigate the CAN logic level and add in a termination resistor
    [MCU_Powertrain.kicad_pcb, MCU_Powertrain.sch]
2020-02-07 Countour and CAN
    - Shrunk board outline
    - Swapped out CAN tranciever
    - Added 5V LDO for CAN outputs, CAN now 5V compatible
    - Checked over layout
    - Everything finished except silkscreen
    [MCU_Powertrain.kicad_pcb, MCU_Powertrain.sch, Powertrain.sch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]
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2020-02-07 Gerbers + Planes
    - Added extra mid layer planes for heatsinking
    - Generated gerbers
    [MCU_Powertrain-B_Cu.gbl, MCU_Powertrain-B_Mask.gbs, MCU_Powertrain-B_SilkS.gbo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]
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2020-02-10 Created Project
    - Created new project that can be independant but not really portable.
    - Need to have motorware installed in te correct C:\ti\ location in order for this to work.
    - workspace is set to the entire "Software" folder
    [main.c]
2020-02-11 Removing Fluff pt.1
    - Removed all DRV8301 references and #IFDEF statements for the DRV8305. Assuming DRV8305 usage for this project.
    - Removed all FAST 1v6 fixes, unnessecary since current version is 1v7
    [main.c]
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2020-02-14 Fixed Footprint and Gerbers
    - Changed mag encoder from 4x4 to 5x5, the correct footprint. :(
    - Updated Gerbers
    [RPM Sensor-B_Cu.gbl, RPM Sensor-B_Mask.gbs, RPM Sensor-B_SilkS.gbo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]
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2020-02-23 Added pie.c and pie.h
    - Added pie.c and pie.h to the local folder since they will be modified to add a 1ms timer.
    - The timer interrupt will be used to send UART data at a fixed rate for proper data collection measurements.
    [main.c]
2020-02-24 Timestamps and CSV Format
    - Timer0 interrupt will NOT work as it overrides the mainISR interrupt. Need to look at doing timestamps instead.
    - Accessed timer2 counter register using "halHandle->timerHandle[2]->TIM"
    - Changed "sendOverUART" to "sendCSV"
    - Added timestamps to sendCSV
    [main.c]
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2020-02-25 Changed DRV8305 CS
    - Updated GPIO19 from SPISTEA to General Purpose in hal.c
    - Also added in GPIO32 as General Purpose for later use in the MCP2515 SPI CS
    - Removed useless GPIO statments
    - Added High and Low set commands to GPIO19 in the DRV8305.c writeSPI and readSPI functions. Measured with a scope to verify that the CS was indeed being pulled low correctly when applied and incorrectly when not applied!
2020-02-28 MCP2515 Library
    - Added and changed MCP2515.c and MCP2515.h and can.h
    - Removed all c++referenes, changed to c format
    - Added MCP handles
    - Added MCP2515 HAL functions HAL_setupMCP2515
    - Also added MCP2515 initialization to HAL_init
    - No compiler errors or syntax errors, although no CAN is officially tested yet
    - Motor still runs after additions
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2020-03-19 Created Project and Schematic Changes
    - Copied MCU_Powertrain project and renamed it
    - Removed all dev components from project and other unnessecary components.
    - Changed cap bank to all 22uF ceramic caps
    [3020-10-0100-xx.SLDPRT, 3020-10-0100-xx.STEP, 3020-10-0100-xx.igs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]
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2020-03-24 Data Logging
    Doing some data logging, had to fix user params
    [main.c]
2020-03-25 3V3 Regulator
    - Added in new 3V3 switching regulator, should save $$$ from the old one and about 1W versus a standard LDO
    [2x2_chip.SLDPRT, 2x2_chip.STEP, Thruster_Controller.kicad_pcb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]
2020-03-29 More Layout and Routing
    - Powertrain is mostly done, very tight and the phase and bus pads are sized and placed!
    [Powertrain.sch, Thruster_Controller.kicad_pcb, Thruster_Controller.sch]
2020-03-30 More Layout + Routing
    - Added 3V3 converter
    - Moved DRV passives to directly underneath DRV chip on top layer
    - Fit power indication LEDs!
    - Think there should be enough space for everything! Routing to the left of TI chip and CAN controller to the right
    [Thruster_Controller.kicad_pcb, Thruster_Controller.sch]
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2020-03-31 Silk and Routing
    - Fixed 5V LED indicator
    - Small layout and routing cleanups
    - Cleaned up Silkscreen
    - Board is "finished" !!
    [Powertrain.sch, Thruster_Controller.kicad_pcb, Thruster_Controller.sch]
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2020-04-05 Changed Cap Bank + Gerbers
    - Changed cap bank to 3 aluminum poly caps plus 3 ceramic caps
    - Fixed routing
    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
    [Powertrain.sch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]
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2020-04-05 3D Model
    - Had to do some trickery to get the model exported and close to the real thing.
    - Need to be very cautious in tolerance when doing up CAD work
    [Thruster_Controller.SLDASM, Thruster_Controller.kicad_pcb]
2020-04-06 New Gerbers
    - Fixed some small errors in silkscreen on the thruster controller
    - Moved the programming header further from the edge, should help mechanically
    [Thruster_Controller-B_Cu.gbl, Thruster_Controller-B_Mask.gbs, Thruster_Controller-B_SilkS.gbo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]
2020-05-04 CAN Testing
    - Still need to fix CS issue and see where that takes it
    [main.c]
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2020-08-22 Initial Routing and Layout
    - Completed all routing, all connections made and zero DRC errors.
    - Some courtyard errors but they are irrelevant
    [Thruster_Controller_V2.kicad_pcb]
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2020-09-05 VDD fix
    - Fixed VDD error, disconnected it from 3V3 rail.
    - Will add any more updates to V2.1 after V2 testing
    [TI_MCU.sch, Thruster_Controller_V2.kicad_pcb, Thruster_Controller_V2.sch]
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2020-09-05 Updated is05_motor_id.c
    - Removed reference to induction motors, pwmdac, and data logging to shorten code
    - Added reference to the test led on the board for proper blinky.
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2020-09-09 Added FIles and Debug
    - Added more files and fixed debug configuration, which wasn't carried over
    [main.c]
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2020-09-10 Started CAN updates
    - Need to fix CAN transciever, add 5V rail!
    - Also subbing in a new transciever that is a newer PN and is lower in cost.
    [Thruster_Controller_V2.sch]
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2020-09-10 Fixed CMPSS
    - Fixed CMPSS issue! Need to use trip 7,8,9! No superflurous OC trips like in the TI thread either, at least so far.
    - Removed some unnessecary comments.
2020-09-10 CMPSS still giving issues lol
    - Okay so that didn't work
    - Commenting out setupFaults for now, as it just causes trouble.
    - Must be the CMPSS ......
    [main.c]
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2020-09-18 Layout Changes
    - Flipping 3V3 regulator to the bottom of the board for better thermal performance.
    - Likewise placing 5V regulator on the bottom. This will require mech changes.
    - Need to compress things to the right more
    [Thruster_Controller_V2.kicad_pcb]
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2020-09-20 Silk and touchups
    - Updated aluminum poly cap, adjusted courtyard
    - Fixed silkscreen
    - Added more power planes near LDOs
    - Cleaned up some routing, still need to have a gooood look before sending this off. But, its 99% ready to go!
    [Powertrain.sch, Thruster_Controller_V2.kicad_pcb]
2020-11-23 Updated Footprints
    - Moved over to the default KiCAD footprints, the rounded ones.
    - Updated all 3D models as well
    - Need to fix a bunch of DRC errors ;(
    [Powertrain.sch, TI_MCU.sch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]
2020-11-23 DRC
    - Fixed all new DRC errors created by new footprints.
    [Thruster_Controller_V2.kicad_pcb]
2020-11-23 V2.1
    - Fixed silk
    - Cleaned up routing
    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
    [Thruster_Controller_V2-B_Cu.gbr, Thruster_Controller_V2-B_Paste.gbr, Thruster_Controller_V2-B_SilkS.gbr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]
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2021-01-16 Fixed a woopsies
    - Change R7 from 0402 to 0603 for future board spins
    [Thruster_Controller_V2.kicad_pcb, Thruster_Controller_V2.sch]
2021-01-17 Got it
    - Had to reinstall motorcontrol SDK in the CSS resource explorer. Didn't recognize that it was already installed
    [Thruster_Controller_V2.kicad_pcb]
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2021-02-08 Removed Extra Code
    - Deleted some things that will not be used in order to shorten up the code
    - Induction motor references, PWMDAC, etc
    [main.c]
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2021-02-10 CAN Telemetry Start
    - Removed some more datalog / pwmdac stuff
    - Added define for the frequency of the CAN telemetry.
    - Added send code for measured RPM
    - Not sure if highbyte / lowbyte / direction order is correct. Need to figure that out!
    [main.c]
2021-02-10 Fixing Sending
    - Moved CAN object definitions to setupCANB function in hal.c. This way they occur before CAN_start like in the example code
    - Added in new ReadCANwithID function from updated can.c library
    - CAN works now, but it sends as fast as possible and forever with one CANsend() function call!
    [main.c]
2021-02-10 Sending verified!!!
    - Tested can_ex1 and it works as expected, need to find the difference between that code and my main code to fix the issue!
    - It was the ACK bit!! Needed another CAN node in order to create the ACK bit. Only scoping the bus causes no ACK bit, therefore the controller keeps sending the message until it sees an ACK bit.
    [can_ex1_loopback.obj, device.obj, f28004x_codestartbranch.obj]
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2021-02-11 Tested CAN, Updated Functions
    - Testing CAN
    - Added proper 'motor enable' flag lol
    - Changed fault.all to fault.bit, fault.all is 1 if there is any fault
    - Fixed voltage and torque sending commands, verified the math with the received values : )
    [main.c]
2021-02-11 Flash Configuration
    - Fixing the flash config linking errors so I can actually program these boards lol.
    - Just had to update the includes in the project settings to be the same as the RAM config.
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2021-02-13 Tuned T200
    - The motor ID is super buggy but I got some parameters that should work. Rs is a lot lower than before obviously, about 0.09 ohm.
    Inductance and flux is the same as previous recorded measurements
    [is05_motor_id.c, main.c]
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2021-02-14 Board Programming
    - Finished flashing all the boards.
    - Still getting that high pitch noise when motor is ON, especially at RPM=0. Hard to say what is causing this or if it can even be fixed.
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2021-02-21 Changes from motorcontrol sdk 3.01.00
    - Adding in some changes from the recent motorcontrol sdk 3.01.00.
    - Hoping to see if this fixes some of the CMPSS issues.
    - No CMPSS issues so far on the bench, will need to test this in the tub.
    - This compiles and runs fine.
    [main.c]
2021-02-22 Reduced Kp_Current, Fixed Stability!
    - Recalculated the voltage filter pole, it was slightly off but shouldn't make a big difference.
    - Slightly changed FULLSCALECURRENT to 59.998 from 59.98, recalc and its a bit more accurate now.
    - Reduced Kp_current to over half of its current value (0.370->0.13).
    - Disabled overcurrent bit set since overcurrent trips at 1.5A, do not know why!
    - Reducing Kp_current worked!! Motor can reach high speeds under load and not be unstable! Also standstill high freq noise is reduced substantially, which is amazing.
    [main.c]
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
